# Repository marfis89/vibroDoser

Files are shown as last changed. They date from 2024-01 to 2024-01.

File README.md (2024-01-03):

# Vibrodoser - Open Source Powder Filling Machine  

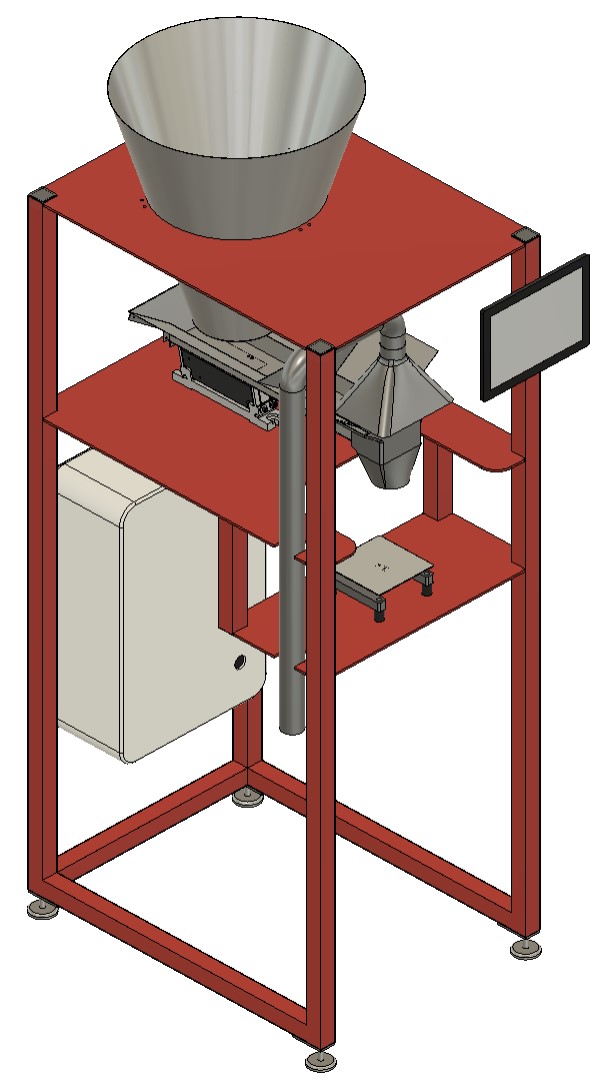
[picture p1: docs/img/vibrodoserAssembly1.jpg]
Vibrodoser Machine


## Introduction  

[Deutsche Anleitung](./GERMANREADME.md)

Vibrodoser is an open-source project aimed at creating a machine for accurately filling bags with various bulk materials such as flour, powder, and other similar substances. This documentation provides a comprehensive guide on the hardware, software, and assembly instructions for replicating the Vibrodoser.

## Features

- Vibrodoser fills up to 1kg bags and containers with precision  
- A linear feeder for a large number of substances  
- Utilizes a Raspberry Pi and Node-RED for control and monitoring
- Incorporates an HX711 board and load cell for accurate weighing
- 3D modeled for easy replication and modifications

## Table of Contents

1. [Parts](#parts)
2. [Hardware Setup](#hardware-setup)
3. [Electrical Setup](#electrical-setup)
4. [Software Setup](#software-setup)
5. [Usage Guide](#usage-guide)
6. [License](#license)

## Parts

To build your own Vibrodoser you will need the following parts. Feel free to use other brands with similar specifications:

### List of electrical parts

- Raspberry pi 3, 4, 5 (price ~50€)
- [Raspberry Pi 8-ch Relay Expansion Board from waveshare](https://www.waveshare.com/rpi-relay-board-b.htm) (price ~25€)
- [1kg load cell with a hx711 A/D hx711](https://www.ebay.de/sch/i.html?_from=R40&_trksid=p2553889.m570.l1313&_nkw=hx+711+loadcell&_sacat=0) (price ~5€)
- [10A Power regulator from kemo](https://www.kemo-electronic.de/en/Transformer-Dimmer/M240-Power-Control-230-V-AC-10-A-Multifunction.php) (price ~50€)
- [Linear feeder from Afag](https://www.afag.com/en/products/detail/linear-feeder-hlf-m-3.html) (get a used one from ebay ~350€)
- [5v ~5a DIN rail power supply HDR-60-5](https://www.meanwell-web.com/en-gb/ac-dc-ultra-slim-din-rail-power-supply-input-range-hdr--60--5) (price ~20€)  
- [13a fuse 1p+N, C-13A](https://www.hager.at/produktkatalog/energieverteilung-und-schutz-schaltgeraete/reiheneinbaugeraete/leitungsschutzschalter/ls-schalter-6ka/mcn513/19391.htm) (price 15€)
- 600mm x 400mm x 200mm control cabinet (price ~80€)
- stuff like cabels, DIN-Rail, wire ducts etc. (price ~50€)

optional for visualisation (you can use your smartphone or laptop too)

- a cheap 10" tablet
- a tablet holder that fits your tablet, so you can mount the tablet to the vibrodoser

### List of 3D models and mechanical parts

- 10m 40mmx40mm steel pipes (price ~200€)
- 5mm steel plate (price ~200€)
  - 2x 600mmx 800mm
  - 1x 280mm x 600mm  

- 1x [big slaughter funnel Ø500mm size 4](https://www.ebay.de/itm/145450569265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) (price ~200€)
- 3x funnel holder (3d print)
- 8x [silent blocks M6 Ø 20 / H 25mm](https://www.ebay.de/sch/i.html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) (price ~20€)
- 4x [machine feet m8](https://www.ebay.de/sch/i.html?_from=R40&_trksid=p2332490.m570.l1313&_nkw=machine+feet&_sacat=0)

optional for dust collection:

- suction funnel (3d print)
- Ø50mm pipe 1000mm  
- Ø50mm pipe 200mm  
- 2x 90° elbow for Ø50mm pipe
- 2x Ø50mm pipe clamp
- vacuum cleaner

optional for wlan / lan connection of the raspberry (You don't have to create a separate network, you can use your normal network too):

- a cheap wlan router (mostly they have 12v input voltage, choose a power supply that fits the router)  
- [12v ~5a DIN rail power supply HDR-60-12](https://www.meanwell-web.com/en-gb/ac-dc-ultra-slim-din-rail-power-supply-input-range-hdr--60--12) (price ~20€)  

## Hardware-Setup

### Frame

To build the frame of the vibrodoser you need to cut the 40mmx40mm pipes into the following dimensions:

- 4x 1600mm
- 2x 720mm
- 2x 255mm
- 1x 520mm

Weld the pipes and plates together, as you can see in the sketch or 3d model. Make sure everything is perfectly aligned and straight. The cutouts from the plates fits the pipes and should help with the alignment. Weld the footplate to the frame so you can attach the machine feet to the frame. To protect the frame and give your vibrodoser a unique look, you should paint the frame in your favorite color.  

optional to close the top end of the pipes you can print these pipe covers four times:

[pipe caps](./cad/3dPrint/Frame/PipeCover.3mf)

### Funnel / Reservoir

Print the [funnel holder](./cad/3dPrint/Frame/FunnelHolder.3mf) three times. Attach the funnel holders to the frame. Place and align the funnel to the frame. Mark and drill three holes to mount the funnel to the frames (M6x20).

### feeder gutter

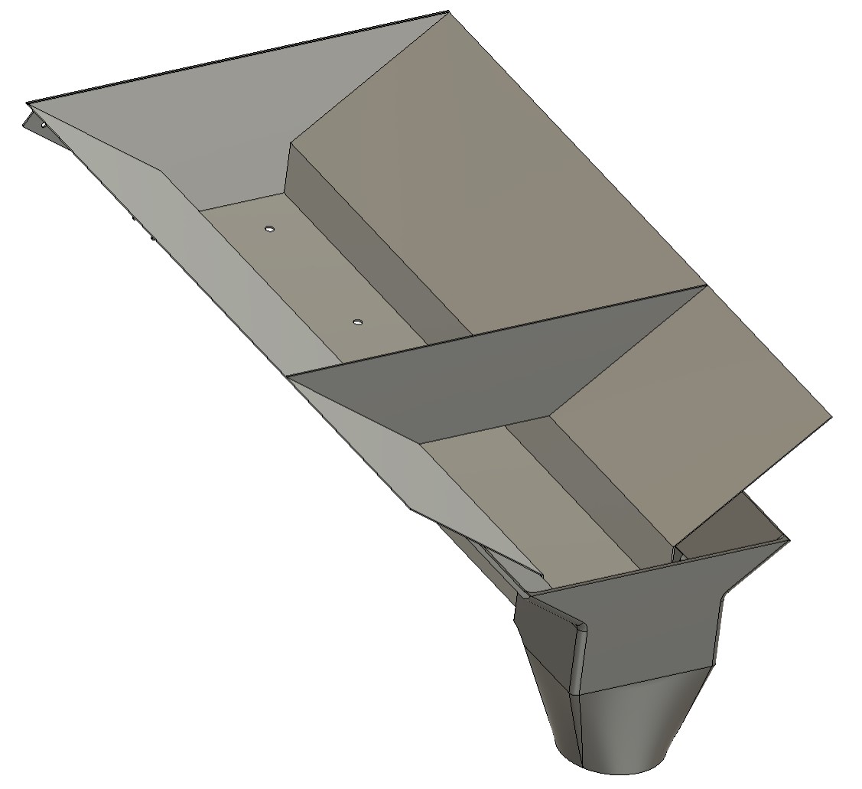
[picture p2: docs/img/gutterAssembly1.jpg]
Gutter


To build the gutter use a 1mm stainless steel plate. Cut and bend the parts into dimensions.  

- [Gutter Base](./cad/dxf/GutterBase.dxf)
- [Gutter Back](./cad/dxf/GutterBack.dxf)

You can weld the stainless steel plates together or just use screws. If you want to use screws, drill holes to the gutter. Because of the vibration, make sure you use screw glue or self-locking nuts. The "smoother gate" in the front is optional. It will help to achieve a smooth level of powder.  

- [Gutter Smoother Gate](./cad/dxf/GutterSmootherGate.dxf)

In order to fill powder into bags, you can print a funnel. It will help to minimize losses of powder.  

- [Gutter Funnel](cad\3dPrint\Gutter\gutterFunnel.3mf)

Assemble the gutter with the linear feeder and mount the linear feeder to the frame.

### Assembly the scale

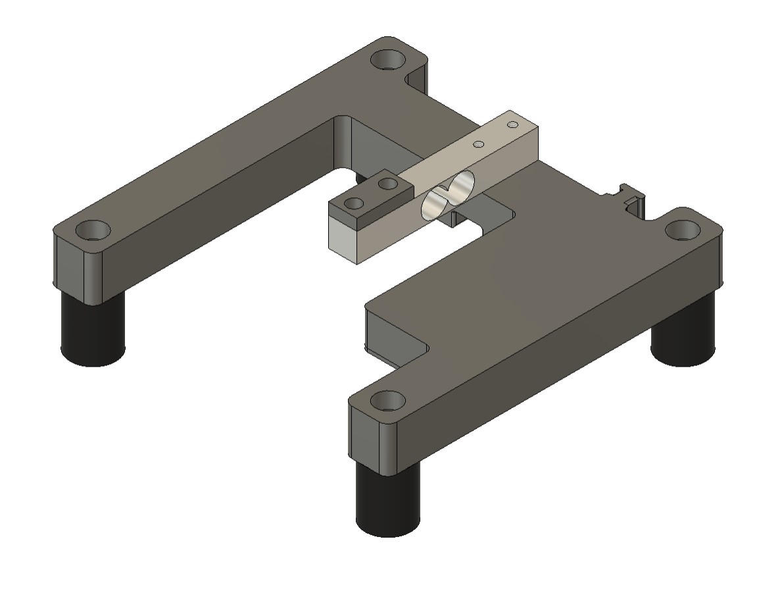
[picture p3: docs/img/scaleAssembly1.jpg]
Scale


To assemble the scale you will need to print three parts:

- [ScaleBase](./cad/3dPrint/Scale/ScaleBase.3mf)
- [hx711Cover](./cad/3dPrint/Scale/hx711Cover.3mf)
- [ScaleDistance](./cad/3dPrint/Scale/ScaleDistance.3mf)

optional you can print the scale plate too, but its recommended to use a stainless steel plate:

- [ScalePlate](./cad/3dPrint/Scale/ScalePlate.3mf) or [ScalePlate](./cad/dxf/ScalePlate.dxf)

First screw the load cell onto the base (2x M5x25). Screw the hx711 board onto the hx711 cover (2x M3x8 and nuts). Shorten the cables of the load cell and solder them with the hx711 board  

Normally:  

- red wire to +E
- black wire to -E
- green wire to +S
- white wire to -S

Make sure this connection fits the manufacturer's specifications of your load cell. Solder a cable with 4 strands to the hx711 board and make sure the cable is long enough to reach the raspberry pi.  

- Vcc to 5v from the pi or power supply
- Gnd to Gnd from the pi or power supply
- DT to Pin 22 (BMC GPIO 25)  
- SCK to Pin 23 (BMC GPIO 11)  

Screw the hx711 cover to the base (4x M3x20). Finally screw the scale plate to the load cell with the scale distance between (2x M4x19). If no data arrives in nodered, check the cabling.

The scale fits to the scale frame plate. Screw the dumpers between the plate and the scale to protect the scale from vibrations.

## Electrical-Setup

WARNING electrical installation are dangerous. If you don't know how to handel this task, ask a professional to do the job for you ! Liability for damages is excluded !

Make three inputs for phase, neutral and earth. Place the 13a input fuse (1p+N) onto the DIN rail and hook phase, neutral to it. Then make a connection from the fuse to the power supplies. Also wire  the phase to relay 1 and relay 2 of the raspberry relay board. We will use the relays to switch the power of the power regulator and the optional vacuum cleaner. Use the NC connection of the relays, so the power is normally cut off. Wire the switched phase und neutral to the power regulator. Wire the linear feeder to the power regulator. Connect the pwm pin 12 (BCM GPIO 18) to the pwn pin of the power regulator. Make sure the pi and the power regulator using the same GND.  

For the optional vacuum cleaner you can install a power outlet, so you can plug you vacuum cleaner into the outlet. Wire the power outlet to the second switched phase and neutral and earth.  

Power the pi or the board with 5v and GND from the power supply. If you choose a separate router setup, connect router and the power supply. Hook up the pi to the router or your local network. You can choose a wlan connection to, but network cables are always the better choice. Connect the four cables of the scale to the pi as described in the previous paragraph.

It also important to hook earth to the frame, first for safety reasons, second to prevent dust explosions.

### Wiring diagrams and schematics of the control cabinet

follow soon

## Software Setup

### Raspberry Pi Configuration

Try to use a good quality usb stick, instead of a simple sd card. There's a lot of tutorials to boot the pi 3 from a usb stick. The pi 4 and up, support usb boot out of the box. Flash the latest raspberry pi os to the stick and power up the pi.  

#### Steps to set up Raspberry Pi

1. Create a directory with ```mkdir /home/pi/vibrodoser```  
2. Copy [hx7111](hx711/hx711.py) and [vibrodoser.py](./hx711/vibroDoser.py) to the pi /home/pi/vibrodoser/
3. Make vibrodoser.py executable ```chmod +x /home/pi/vibroDoser/vibroDoser.py```  
4. Add the content of the [vibrodoser.service](./service/vibrodoser.service) file to /etc/systemd/system/vibrodoser.service
5. Enable the service with ```sudo systemctl enable vibroDoser.service```
6. Start the service with ```sudo systemctl start vibroDoser.service```
7. Check the service with ```sudo systemctl status vibroDoser.service```

The service execute the vibroDoser.py script on boot and take care of a reboot is necessary.

#### Installation of Node-RED and necessary packages

[official tutorial](https://nodered.org/docs/getting-started/raspberrypi)  

```console
sudo apt-get update && sudo apt-get upgrade && \
bash <(curl -sL https://raw.githubusercontent.com/node-red/linux-installers/master/deb/update-nodejs-and-nodered) && \
sudo systemctl enable nodered.service && \
sudo reboot
```

When browsing from another machine you should use the hostname or IP-address of the Pi: http://<hostname>:1880. You can find the IP address by running hostname -I on the Pi.  

Now install the following pallets for nodered dashboard and mqtt broker

-[node-red-contrib-aedes](https://flows.nodered.org/node/node-red-contrib-aedes)  
-[node-red-dashboard](https://flows.nodered.org/node/node-red-dashboard)  

Now import the [flow](./flow/flow.json) to nodered. See this instructions [Importing and Exporting Flows](https://nodered.org/docs/user-guide/editor/workspace/import-export)

#### Node-RED Flow

The flow provides a mqqt broker to communication with the scale service. The flow listening on ```vibroDoser/scale/load``` and sending the tare command on ```vibroDoser/scale/tare``` to the scale. While there is active, all measurements from the scale are blocked.

## Usage Guide

Power on the Vibrodoser. Wait until the nodered dashboard (http://<hostname>:1880/ui) is reachable. The first thing is to tare the scale. Place your bag or container on the scale and hit the "tare" button. Now set the target weight (100g-1000g). You are now good to fill the bag automatically. The feeder slows down, when the weight hits 80% of the target weight. After the filling is complete, remove the bag and check the weight with a calibrated scale. If you are happy with the result, you can fill more bags, if not decrease the target weight or the speed of the feeder (10%-100%). Sometimes you have to play with the settings, until you find a satisfactory result. The consistency of the powder, humidity and temperature have a major influence on the flowability of the powder.  

Finally, some safety information. If your work with powder, watch out for dust. Dust can lead to dust explosions. Use a good vacuum cleaner to avoid too much dust.

Enjoy your vibrodoser und increase the productivity of your company

## License  

Vibrodoser is licensed under the GNU GENERAL PUBLIC LICENSE. Please refer to the [LICENSE](LICENSE) file for more details.

If you distribute copies of such a program, whether gratis or for a fee, you must pass on to the recipients the same freedoms that you received. You must make sure that they, too, receive or can get the source code. And you must show them these terms so they know their rights as Outlined in the GPLv3 License.

THIS SOFTWARE IS PROVIDED BY THE COPYRIGHT HOLDERS AND CONTRIBUTORS "AS IS" AND ANY EXPRESS OR IMPLIED WARRANTIES, INCLUDING, BUT NOT LIMITED TO, THE IMPLIED WARRANTIES OF MERCHANTABILITY AND FITNESS FOR A PARTICULAR PURPOSE ARE DISCLAIMED. IN NO EVENT SHALL BE LIABLE FOR ANY DIRECT, INDIRECT, INCIDENTAL, SPECIAL, EXEMPLARY, OR CONSEQUENTIAL DAMAGES (INCLUDING, BUT NOT LIMITED TO, PROCUREMENT OF SUBSTITUTE GOODS OR SERVICES; LOSS OF USE, DATA, OR PROFITS; OR BUSINESS INTERRUPTION) HOWEVER CAUSED AND ON ANY THEORY OF LIABILITY, WHETHER IN CONTRACT, STRICT LIABILITY, OR TORT (INCLUDING NEGLIGENCE OR OTHERWISE) ARISING IN ANY WAY OUT OF THE USE OF THIS SOFTWARE, EVEN IF ADVISED OF THE POSSIBILITY OF SUCH DAMAGE.

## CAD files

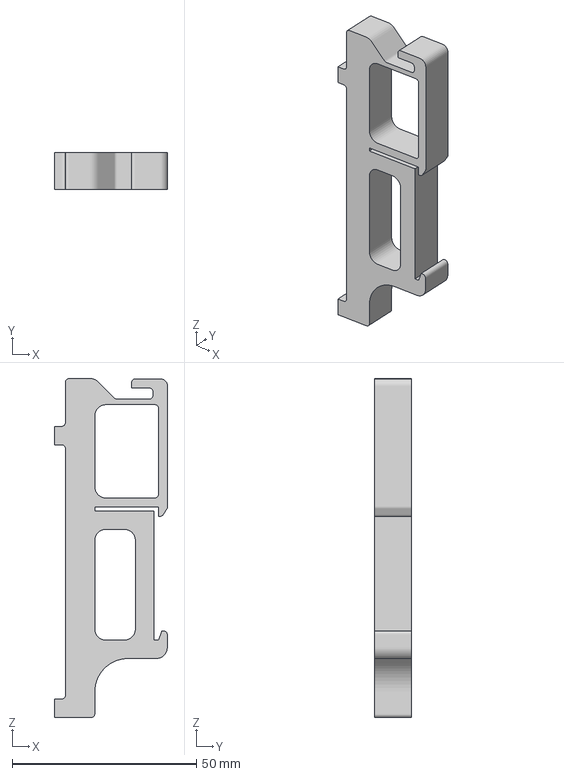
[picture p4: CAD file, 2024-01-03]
cad/3dPrint/controlCabinet/KemoPowerRegulatorDinRail.3mf
30.8 x 10.0 x 92.0 mm

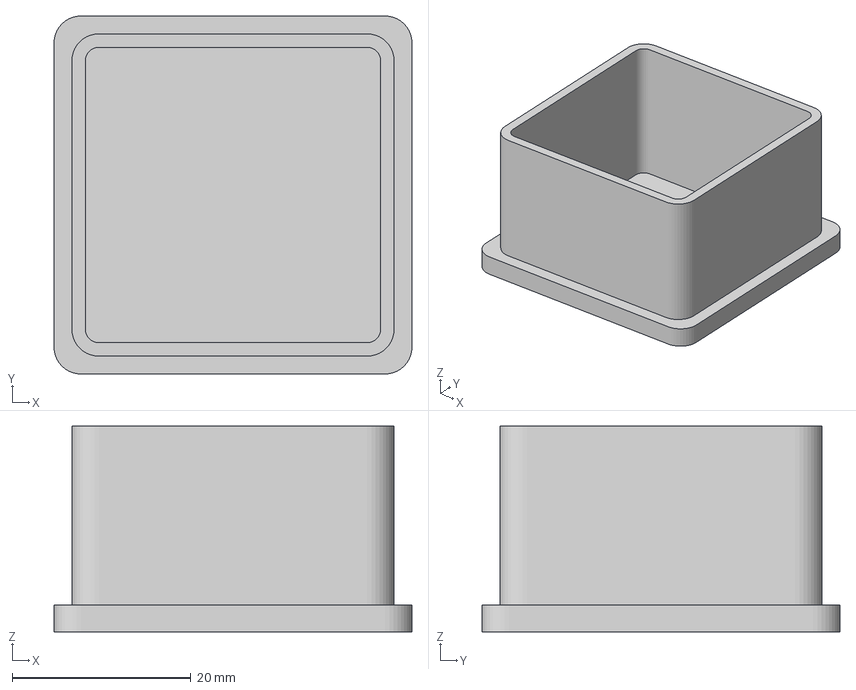
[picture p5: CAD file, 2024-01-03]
cad/3dPrint/Frame/PipeCover.3mf
40.0 x 40.0 x 23.0 mm

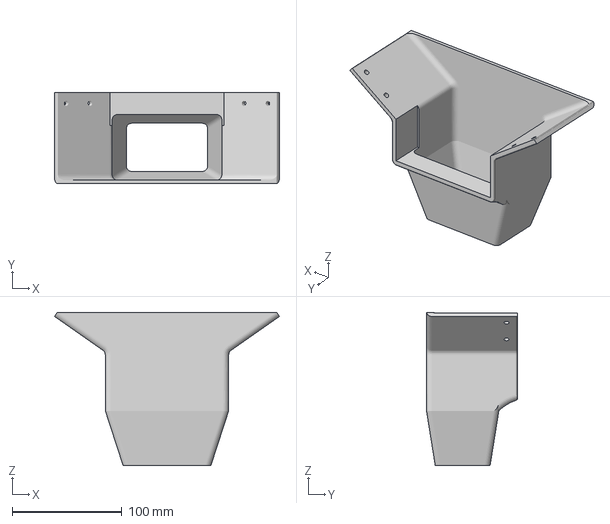
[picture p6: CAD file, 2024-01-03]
cad/3dPrint/Gutter/gutterFunnelSquare.3mf
205.2 x 83.0 x 139.8 mm

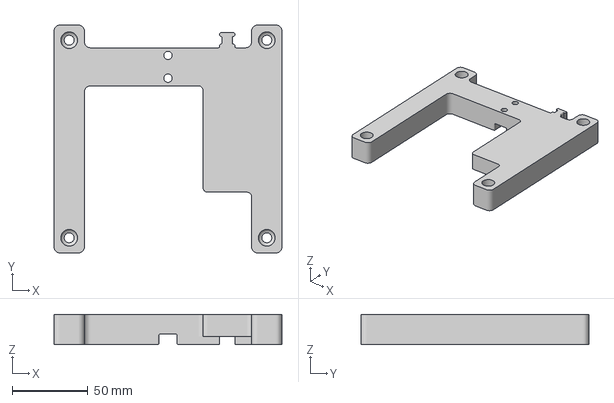
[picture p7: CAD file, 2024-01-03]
cad/3dPrint/Scale/ScaleBase.3mf
150.0 x 150.0 x 20.0 mm

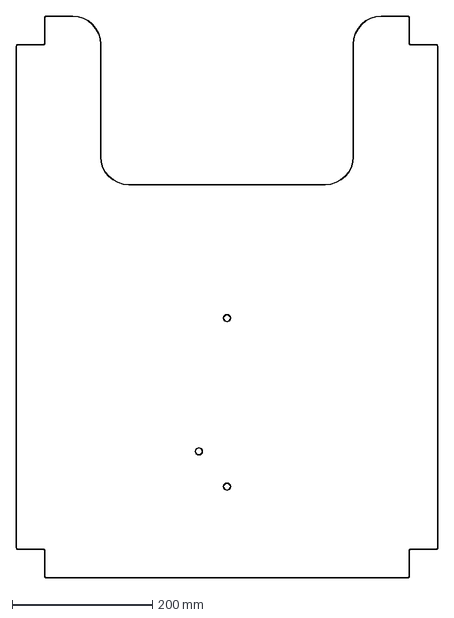
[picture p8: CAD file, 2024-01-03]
cad/dxf/FrameMidPlate.dxf
600.0 x 800.0 mm

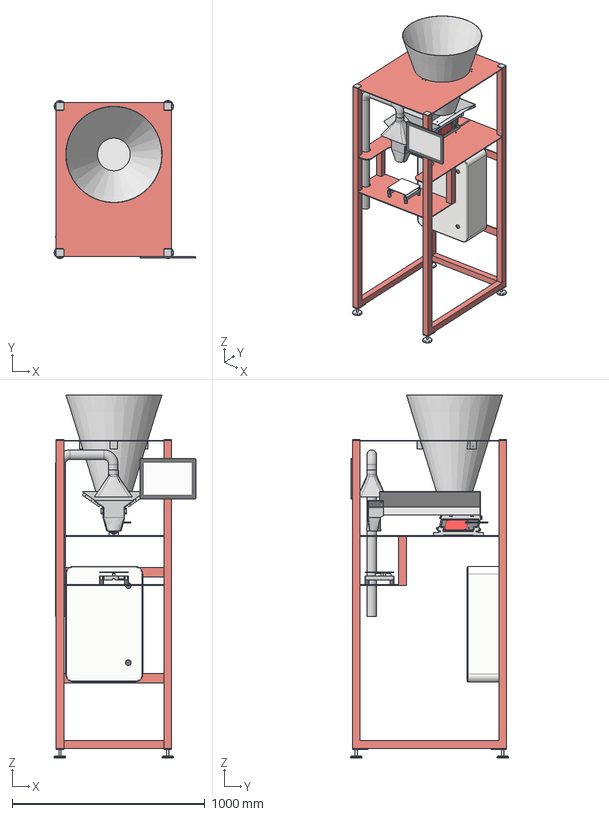
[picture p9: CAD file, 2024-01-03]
cad/vibroDoser.step
735.5 x 820.0 x 1885.0 mm
Schaltschrank
FrameMidPlate
FrameFunnelPlate
ScaleFramePlate
FootPlate x 4
Trichter_groß
Tablet_Lenovo_X1
_50259276 Linear feeder HLF25-M1
_50259276 Linear feeder HLF25-M2
RinneRund
ScaleBase
LoadCell
ScalePlate
PipeCover4040 x 4
FunnelHolder x 3
SuctionFunnel

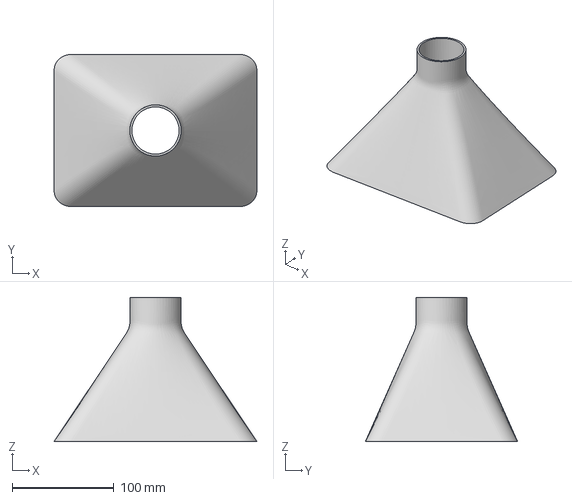
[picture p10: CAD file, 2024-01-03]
cad/3dPrint/Frame/SuctionFunnel.3mf
200.0 x 150.0 x 142.0 mm

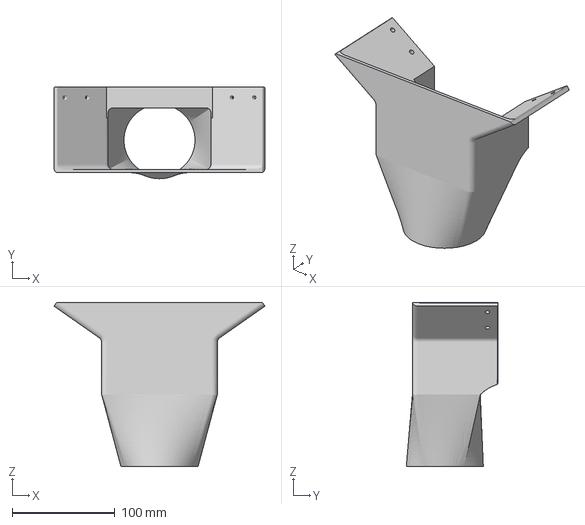
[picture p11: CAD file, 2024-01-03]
cad/3dPrint/Gutter/gutterFunnelRound.3mf
205.2 x 89.0 x 159.8 mm

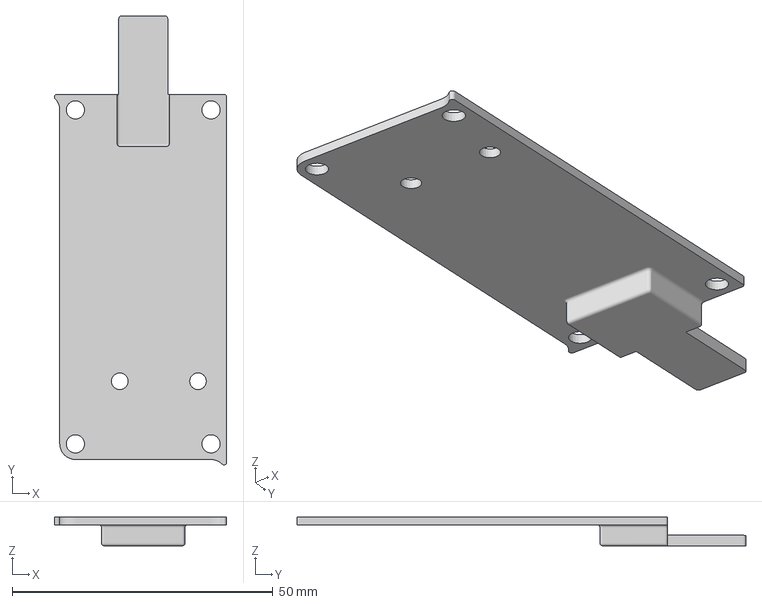
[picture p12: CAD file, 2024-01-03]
cad/3dPrint/Scale/hx711Cover.3mf
33.0 x 86.0 x 5.50 mm

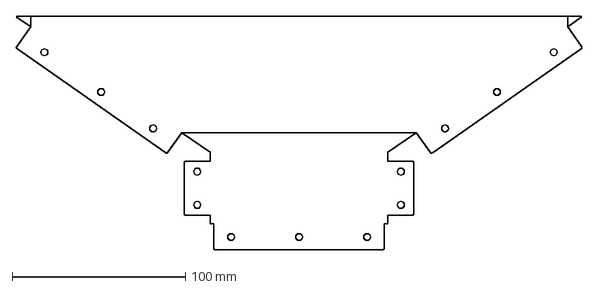
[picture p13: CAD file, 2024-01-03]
cad/dxf/GutterBack.dxf
326.5 x 135.0 mm

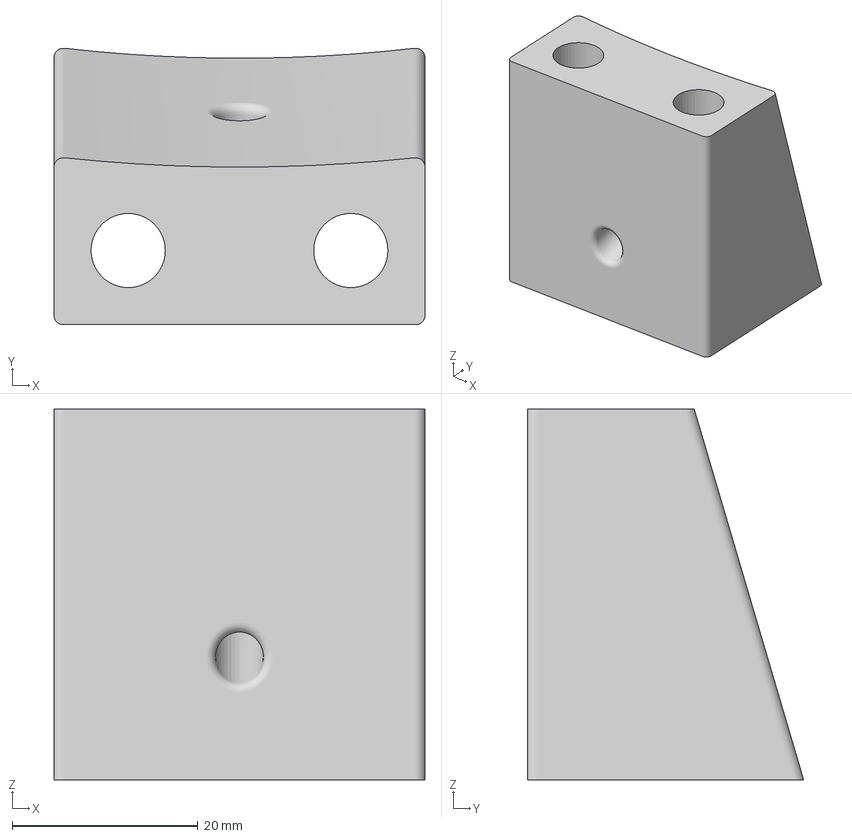
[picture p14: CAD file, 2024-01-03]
cad/3dPrint/Frame/FunnelHolder.3mf
40.0 x 29.8 x 40.0 mm

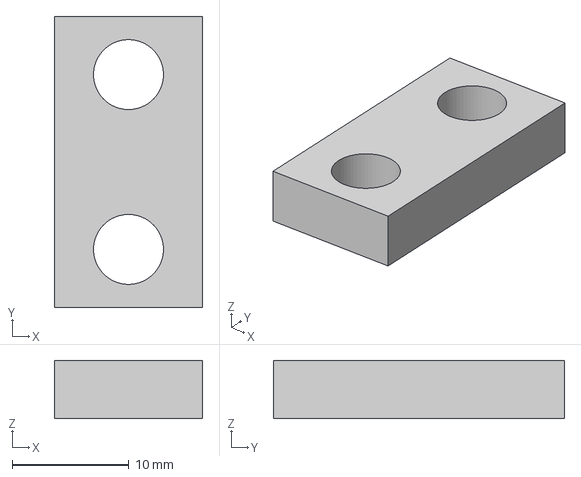
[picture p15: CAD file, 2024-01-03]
cad/3dPrint/Scale/ScaleDistance.3mf
12.7 x 25.0 x 5.00 mm

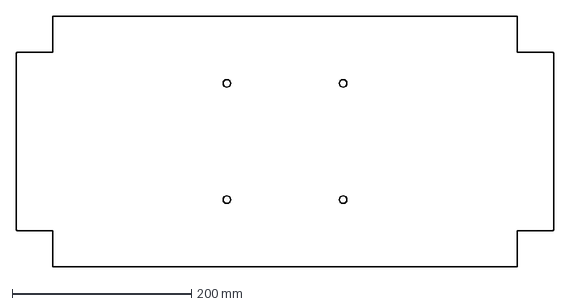
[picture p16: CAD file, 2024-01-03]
cad/dxf/ScaleFramePlate.dxf
600.0 x 280.0 mm

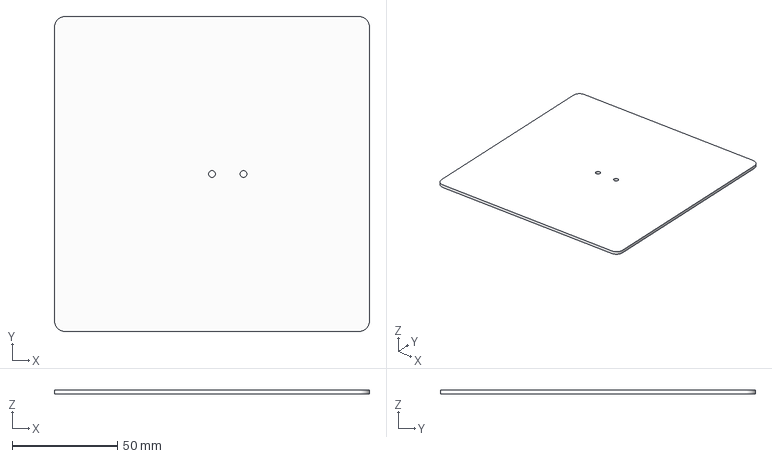
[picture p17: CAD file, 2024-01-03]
cad/3dPrint/Scale/ScalePlate.3mf
150.0 x 150.0 x 2.00 mm

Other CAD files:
cad/dxf/GutterSmootherGate.dxf
cad/dxf/ScalePlate.dxf
cad/dxf/FrameFunnelPlate.dxf
cad/dxf/FootPlate.dxf
cad/dxf/GutterBase.dxf
cad/vibroDoser.f3z

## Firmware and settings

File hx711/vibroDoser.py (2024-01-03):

#!/usr/bin/python3
import sys
import time
import paho.mqtt.client as mqtt # mqtt libary 
from hx711 import HX711 # https://github.com/tatobari/hx711py

# The callback for when the client receives a CONNACK response from the server.
def on_connect(client, userdata, flags, rc):
    if rc == 0:
        print("Connected to MQTT broker")
    else:
        print("Failed to connect to MQTT broker, return code %d\n", rc)

    client.subscribe(list_2_subscribe)

def on_message_set_tare_mqtt(client, userdata, msg):
    try:
        decode_string=str(msg.payload.decode("utf-8","ignore")) 
        print("on_message_set_tare_mqtt: ", decode_string)   
        hx711ReferenceUnit = int(decode_string)
        set_tare(hx711ReferenceUnit)

    except Exception as e:
        print(e)
    finally:
        pass    

def set_tare(hx711ReferenceUnit):

    global scaleStatus

    scaleStatus = False

    print("Start tare !...")

    hx.set_reference_unit(hx711ReferenceUnit)

    hx.reset()

    hx.tare()  

    client.publish(mqtt_broker_topic_scaleStatus, True)

    print("Tare done")

    scaleStatus = True
 

def main():    

    # init tare on start
    set_tare(hx711ReferenceUnit)
    
    last_weight = 10


    while True:
        try:

            if scaleStatus:               
                # calc the load
                weight = round(hx.get_weight(3))               

                if weight != last_weight:
                    print("weight: %s [g]" % (weight))

                    client.publish("vibroDoser/scale/load", weight)
                    last_weight = weight

                hx.power_down()
                hx.power_up()

            time.sleep(0.01)

        except Exception as e:
            print("Vibrodoser Exception: ", e)
            break

        except (KeyboardInterrupt, SystemExit):
            print("Vibrodoser KeyboardInterrupt")
            break  

    client.loop_stop()
    print("exit vibroDoser loop!")
    sys.exit(1)
        
if __name__ == "__main__":

    global scaleStatus

    mqtt_broker_topic_tare = "vibroDoser/scale/tare"
    list_2_subscribe = [(mqtt_broker_topic_tare,2)]

    mqtt_broker_topic_scaleStatus = "vibroDoser/scale/status"

    client = mqtt.Client()

    client.on_connect = on_connect
    client.connect("localhost", 1883, 60)

    client.loop_start() 

    client.message_callback_add(mqtt_broker_topic_tare, on_message_set_tare_mqtt)

    # HX711 settings
    # The correct calibration of the weight sensor is crucial. 
    # For this we need a reference object whose weight we know. 
    # Select the average value of the maximum (load cell 1 kilogram = 500g reference object) 
    # The displayed values can be positive or negative. 
    # In my case, values around 1298304 were displayed for 503g. 
    # My reference value is therefore 1298304 ÷ 503 = 2581.

    # using pin 22 and 23
    hx = HX711(22, 23) 
    hx711ReferenceUnit = 1946

    hx.set_reading_format("MSB", "MSB")
    hx.reset()

    # start main loop 
    main()

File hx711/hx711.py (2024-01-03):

#!/usr/bin/python3

import RPi.GPIO as GPIO
import time
import threading

class HX711:

    def __init__(self, dout, pd_sck, gain=128):
        self.PD_SCK = pd_sck

        self.DOUT = dout

        # Mutex for reading from the HX711, in case multiple threads in client
        # software try to access get values from the class at the same time.
        self.readLock = threading.Lock()
        
        GPIO.setmode(GPIO.BCM)
        GPIO.setup(self.PD_SCK, GPIO.OUT)
        GPIO.setup(self.DOUT, GPIO.IN)

        self.GAIN = 0

        # The value returned by the hx711 that corresponds to your reference
        # unit AFTER dividing by the SCALE.
        self.REFERENCE_UNIT = 1
        self.REFERENCE_UNIT_B = 1

        self.OFFSET = 1
        self.OFFSET_B = 1
        self.lastVal = int(0)

        self.DEBUG_PRINTING = False

        self.byte_format = 'MSB'
        self.bit_format = 'MSB'

        self.set_gain(gain)

        # Think about whether this is necessary.
        time.sleep(1)

        
    def convertFromTwosComplement24bit(self, inputValue):
        return -(inputValue & 0x800000) + (inputValue & 0x7fffff)

    
    def is_ready(self):
        return GPIO.input(self.DOUT) == 0

    
    def set_gain(self, gain):
        if gain == 128:
            self.GAIN = 1
        elif gain == 64:
            self.GAIN = 3
        elif gain == 32:
            self.GAIN = 2

        GPIO.output(self.PD_SCK, False)

        # Read out a set of raw bytes and throw it away.
        self.readRawBytes()

        
    def get_gain(self):
        if self.GAIN == 1:
            return 128
        if self.GAIN == 3:
            return 64
        if self.GAIN == 2:
            return 32

        # Shouldn't get here.
        return 0
        

    def readNextBit(self):
       # Clock HX711 Digital Serial Clock (PD_SCK).  DOUT will be
       # ready 1us after PD_SCK rising edge, so we sample after
       # lowering PD_SCL, when we know DOUT will be stable.
       GPIO.output(self.PD_SCK, True)
       GPIO.output(self.PD_SCK, False)
       value = GPIO.input(self.DOUT)

       # Convert Boolean to int and return it.
       return int(value)


    def readNextByte(self):
       byteValue = 0

       # Read bits and build the byte from top, or bottom, depending
       # on whether we are in MSB or LSB bit mode.
       for x in range(8):
          if self.bit_format == 'MSB':
             byteValue <<= 1
             byteValue |= self.readNextBit()
          else:
             byteValue >>= 1              
             byteValue |= self.readNextBit() * 0x80

       # Return the packed byte.
       return byteValue 
        

    def readRawBytes(self):
        # Wait for and get the Read Lock, incase another thread is already
        # driving the HX711 serial interface.
        self.readLock.acquire()

        # Wait until HX711 is ready for us to read a sample.
        while not self.is_ready():
           pass

        # Read three bytes of data from the HX711.
        firstByte  = self.readNextByte()
        secondByte = self.readNextByte()
        thirdByte  = self.readNextByte()

        # HX711 Channel and gain factor are set by number of bits read
        # after 24 data bits.
        for i in range(self.GAIN):
           # Clock a bit out of the HX711 and throw it away.
           self.readNextBit()

        # Release the Read Lock, now that we've finished driving the HX711
        # serial interface.
        self.readLock.release()           

        # Depending on how we're configured, return an orderd list of raw byte
        # values.
        if self.byte_format == 'LSB':
           return [thirdByte, secondByte, firstByte]
        else:
           return [firstByte, secondByte, thirdByte]


    def read_long(self):
        # Get a sample from the HX711 in the form of raw bytes.
        dataBytes = self.readRawBytes()


        if self.DEBUG_PRINTING:
            print(dataBytes,)
        
        # Join the raw bytes into a single 24bit 2s complement value.
        twosComplementValue = ((dataBytes[0] << 16) |
                               (dataBytes[1] << 8)  |
                               dataBytes[2])

        if self.DEBUG_PRINTING:
            print("Twos: 0x%06x" % twosComplementValue)
        
        # Convert from 24bit twos-complement to a signed value.
        signedIntValue = self.convertFromTwosComplement24bit(twosComplementValue)

        # Record the latest sample value we've read.
        self.lastVal = signedIntValue

        # Return the sample value we've read from the HX711.
        return int(signedIntValue)

    
    def read_average(self, times=3):
        # Make sure we've been asked to take a rational amount of samples.
        if times <= 0:
            raise ValueError("HX711()::read_average(): times must >= 1!!")

        # If we're only average across one value, just read it and return it.
        if times == 1:
            return self.read_long()

        # If we're averaging across a low amount of values, just take the
        # median.
        if times < 5:
            return self.read_median(times)

        # If we're taking a lot of samples, we'll collect them in a list, remove
        # the outliers, then take the mean of the remaining set.
        valueList = []

        for x in range(times):
            valueList += [self.read_long()]

        valueList.sort()

        # We'll be trimming 20% of outlier samples from top and bottom of collected set.
        trimAmount = int(len(valueList) * 0.2)

        # Trim the edge case values.
        valueList = valueList[trimAmount:-trimAmount]

        # Return the mean of remaining samples.
        return sum(valueList) / len(valueList)


    # A median-based read method, might help when getting random value spikes
    # for unknown or CPU-related reasons
    def read_median(self, times=3):
       if times <= 0:
          raise ValueError("HX711::read_median(): times must be greater than zero!")
      
       # If times == 1, just return a single reading.
       if times == 1:
          return self.read_long()

       valueList = []

       for x in range(times):
          valueList += [self.read_long()]

       valueList.sort()

       # If times is odd we can just take the centre value.
       if (times & 0x1) == 0x1:
          return valueList[len(valueList) // 2]
       else:
          # If times is even we have to take the arithmetic mean of
          # the two middle values.
          midpoint = len(valueList) / 2
          return sum(valueList[midpoint:midpoint+2]) / 2.0


    # Compatibility function, uses channel A version
    def get_value(self, times=3):
        return self.get_value_A(times)


    def get_value_A(self, times=3):
        return self.read_median(times) - self.get_offset_A()
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
